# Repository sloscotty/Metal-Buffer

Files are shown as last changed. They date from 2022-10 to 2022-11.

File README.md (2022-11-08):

# Metal Buffer (for ERCF or other MMU)

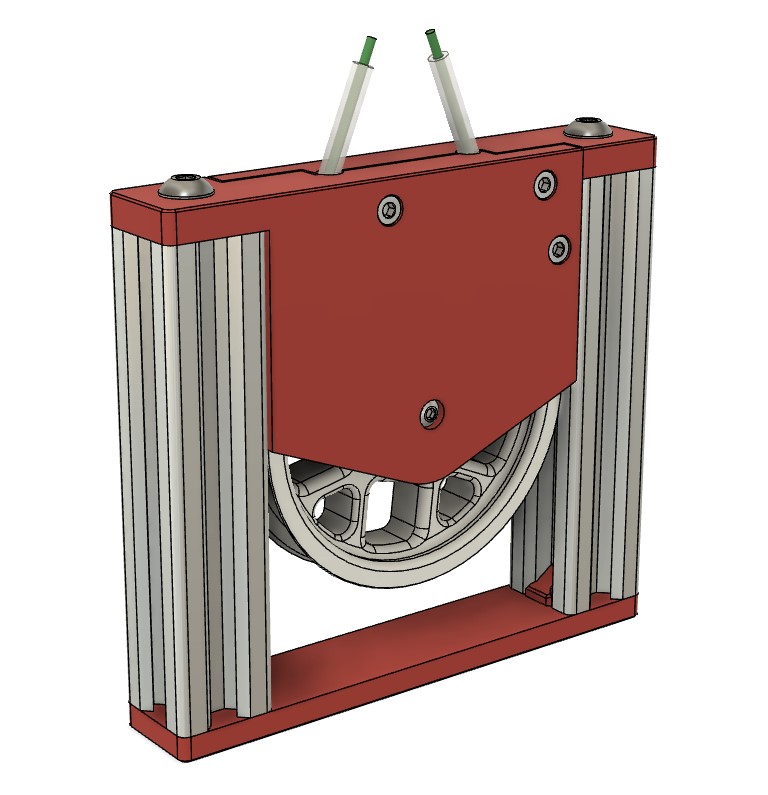
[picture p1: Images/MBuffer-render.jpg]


This is a single-loop buffer that utilizes aluminum extrusion to constrain the filament within the buffer.  It is designed around Openbuilds V-slot extrusion because I had tons of it around.  It also uses the buffer wheel and bearing from the Enraged Rabbit Carrot Feeder project.

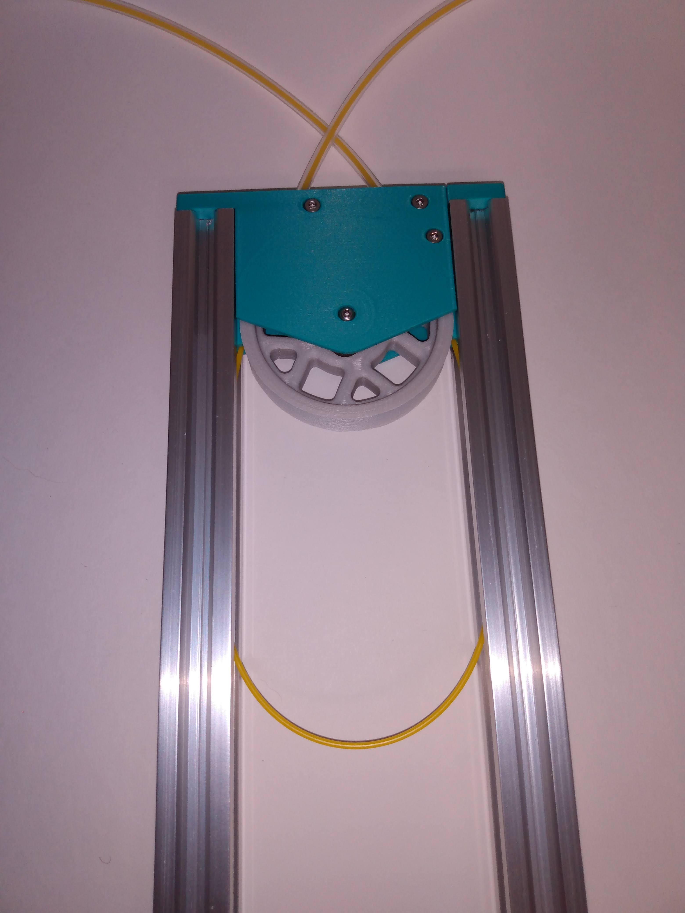
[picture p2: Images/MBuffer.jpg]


The design could probably be modified to work with other 20x20 extrusion, but it would not be a trivial task.  The slot in the top wheel assembly depends on the extra space made available by the "V" slot.  Additionally, the tapered slot provides a natural guide for the filament once it leaves the printed wheel assembly.

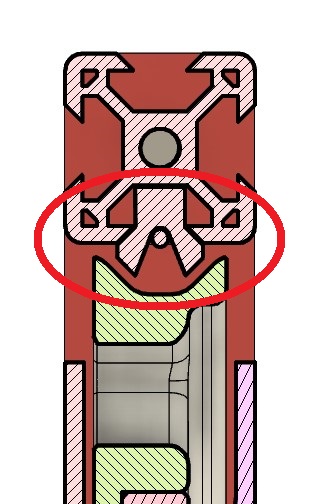
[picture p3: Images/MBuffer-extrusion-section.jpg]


For you ERCF users, V-slot is available in 20x60 (enough for 3 buffers) for about $20/meter. And the spacing almost exactly matches the tool spacing of the ERCF. (It's also available in 20x40 and 20x80.) Here is an example of two buffers mounted in 20x40:

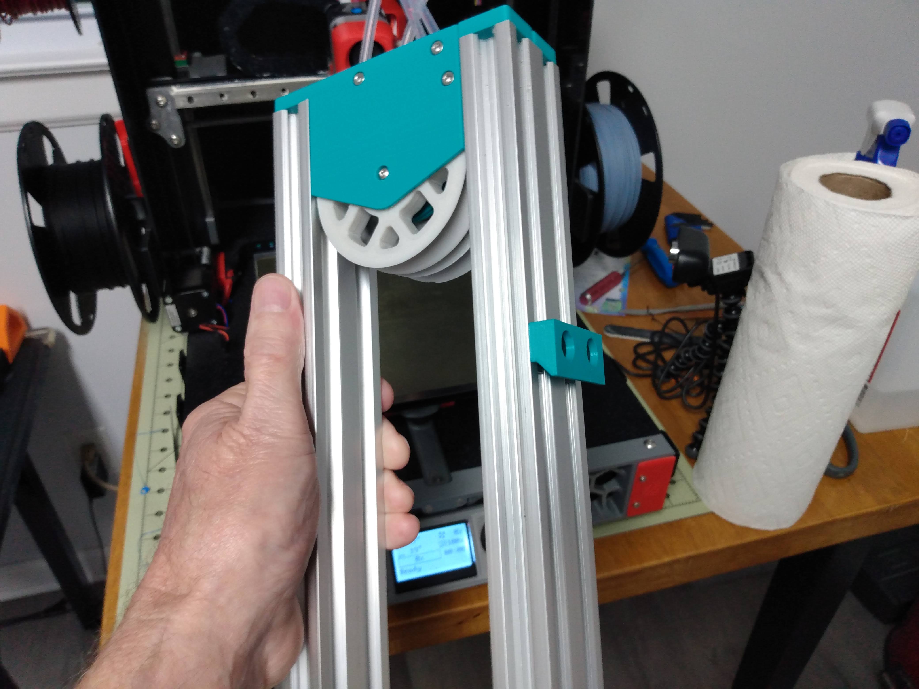
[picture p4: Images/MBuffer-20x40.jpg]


## Determine Extrusion Length

To determine the length of the extrusion required (in mm) use the formula:

**BufferLength/2 + 65** (65mm is the space used by the wheel assembly.)

To determine "BufferLength" for ERCF: add the length of the bowden tube,  the distance from the bottom of bowden tube to the nozzle, and the distance from the top of the bowden tube to the magnetic gate (35mm). Note: configured bowden to nozzle distance may not include distance between extruder gears and bowden.

For example, I'm using ERCF on a Switchwire with an LGX.  My bowden tube is 425mm,  my configured bowden-to-nozzle distance is 82mm (I allowed an additional 8mm for bowden to gears).  So "BufferLength" for me was 425 + 90 + 35 = 550.  Doing the calculations above, my requied extrusion length turned out to be 340mm.  Just to be safe, I cut my extrusions to 350mm.

## BOM (for a single buffer)
 - (2) [V-slot aluminum extrusion of required length](https://openbuildspartstore.com/v-slot-linear-rail-1/)
 - (8) M3 x 5mm x 4mm heat-set insert
 - (4) M3 x 8mm SHCS
 - (2) M3 x 10mm SHCS
 - (1) M3 x 6mm BHCS
 - (1) M3 x 8mm BHCS
 - (2) M5 x 6mm BHCS (or self-tapping screws below)
 - (2) M5 x 10mm BHCS (or thumbscrews or self-tapping screws below)
 - (2) 2.5mm ID x 4.0mm OD PTFE tubes (of appropriate length)
 - (1) 608ZZ Bearing (from ERCP)

### (options)
 - M5 x 0.80 tapping tool (for tapping extrusion)
 - (2) M5 x 10mm x 16mm diam thumbscrews [on amazon](https://www.amazon.com/dp/B07KFV6HW8/) (must be tapped with tool)
 - (4) [#10 x 3/4" Self-Tapping Screws](https://openbuildspartstore.com/self-tapping-screw/) (in case you don't like tapping)
 
**Note 1:** You can use a bit longer screws (1-2mm) than shown **except** for the M3 BHCS (axle screws).

**Note 2:** The top assembly *clamps* the PTFE tubing in place. Use of less than 2.5mm ID risks "choking" the filament.

## Directions

Print the parts using standard Voron settings (40% infill, 0.2 layerheight, 0.4 forced extrusion width) out of ABS or ASA.

The Documentation folder contains the [assembly instructions](./Documentation/MBuffer-Assembly.pdf).

## Loading the Buffer

The top of the buffer assembly can be removed for loading if required.  Depending on how you mount your array of buffers, the buffer can be loaded without removing the top.

Here are three modules, each with two buffers mounted in 20x40 extrusion. Each module will stay together even with one top removed for loading.  However, I usually load without removing a top (or even lifting a module - I can reach to the middle of my array easily enough).

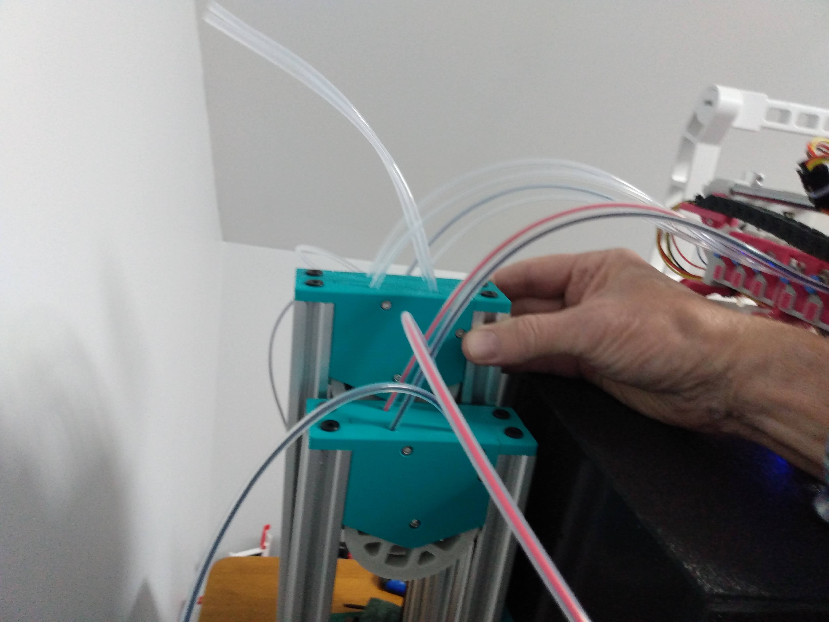
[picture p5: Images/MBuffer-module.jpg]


## How it works and mounting recommendations/caveats (example: MBuffer on Switchwire with 6-cart ERCF)

The filament paths in the buffer's top-assembly are actually straight (as shown in the cross-section). This forces the filament to the extrusion during unloading. Ideally, the resulting tension causes the filament to stay in both extrusions during the load and unload.

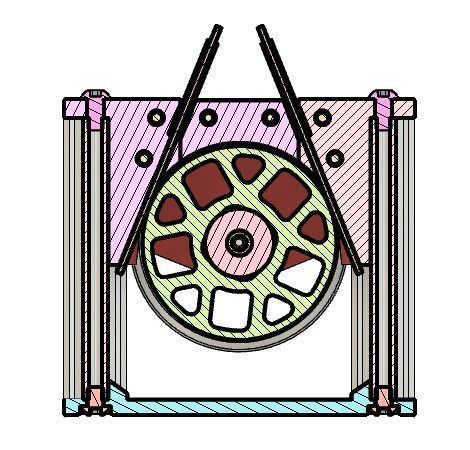
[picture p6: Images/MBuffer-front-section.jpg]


However, excessive "twisting" of the filament (from elsewhere in the system) can cause the filament to pop out of the extrusion.  Therefore positioning the buffer in order to reduce filament twist is essential.  Ideally you want the buffer assembly to be mounted directly behind the ERCF with each buffer aligned with one of the carts.  Even better if you can have your spools mounted behind the buffers.

Here is my current mounting on Switchwire.

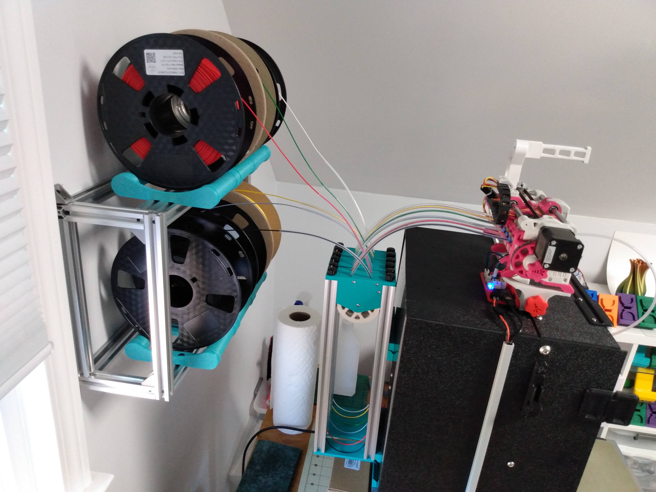
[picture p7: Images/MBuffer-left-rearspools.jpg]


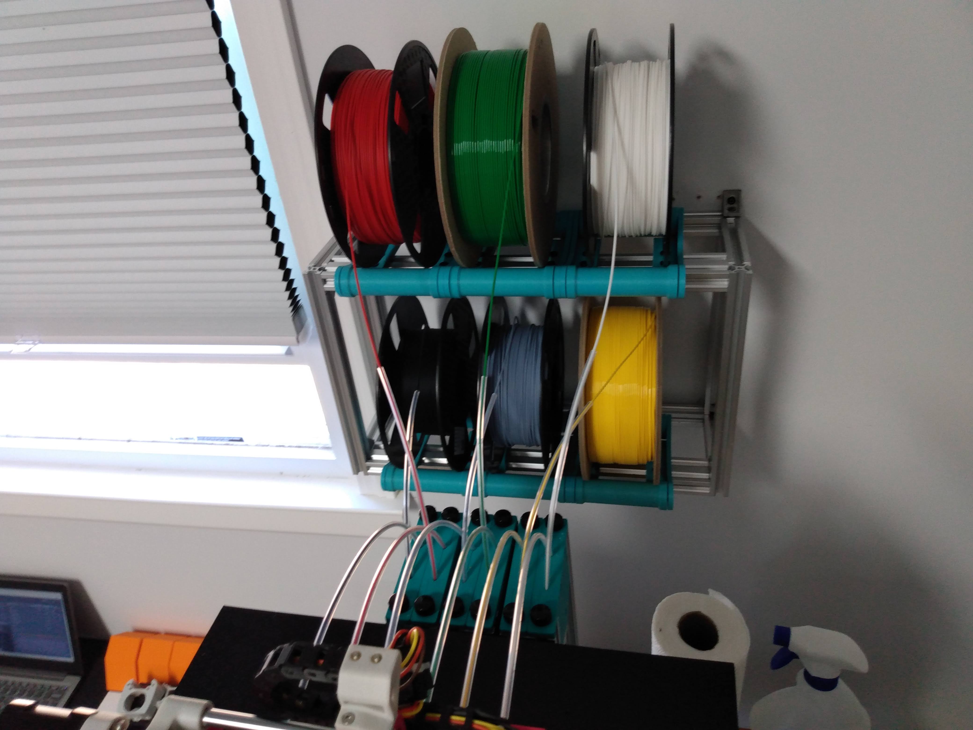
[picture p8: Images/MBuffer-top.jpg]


I originally had my spools routed to the buffers from the sides, but never did have problems with popping filament.  But I am only buffering ~600mm of filament.  A V2 buffering 1100-1200mm will require more care.  Thanks to garbqgebag on discord for beta-testing this design with a V2 and pointing out the importance of mounting position.  See our discussion on the Voron discord: https://discord.com/channels/460117602945990666/909743915475816458/1039285958933225603

### And finally, Metal Buffer in action!

https://user-images.githubusercontent.com/12124123/196645301-cd481165-e586-41fb-b28d-ce4f89cd5ee8.mp4

Enjoy!

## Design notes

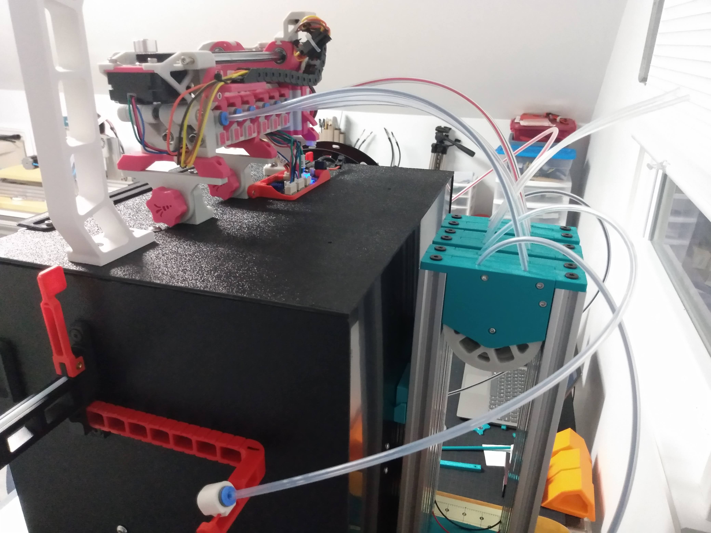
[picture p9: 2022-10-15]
Images/MBuffer-right.jpg

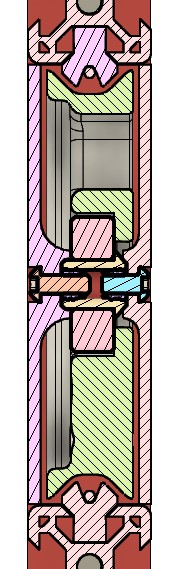
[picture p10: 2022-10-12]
Images/MBuffer-cross-section.jpg

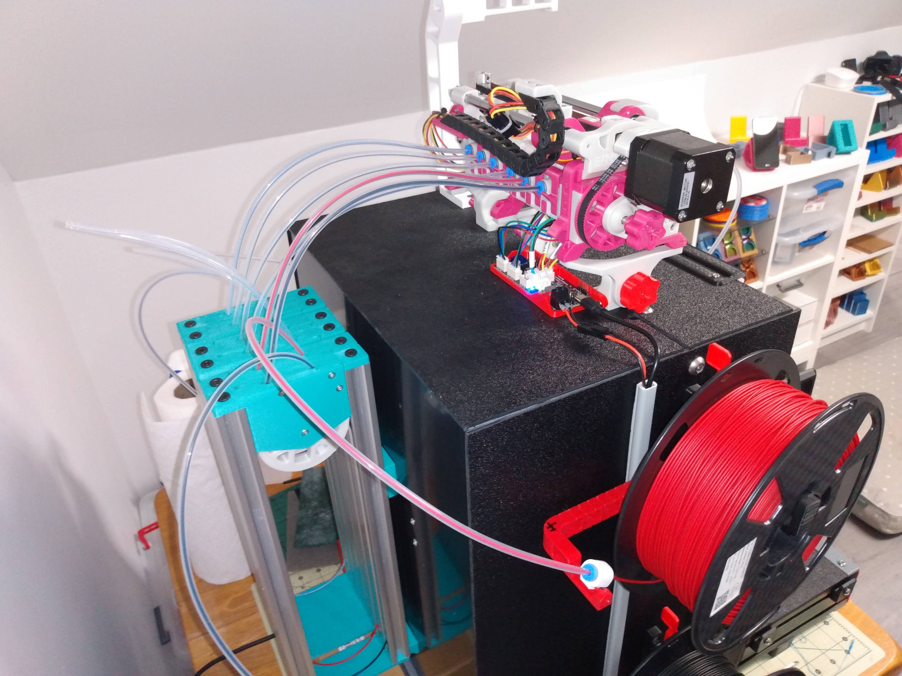
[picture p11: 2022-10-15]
Images/MBuffer-left.jpg

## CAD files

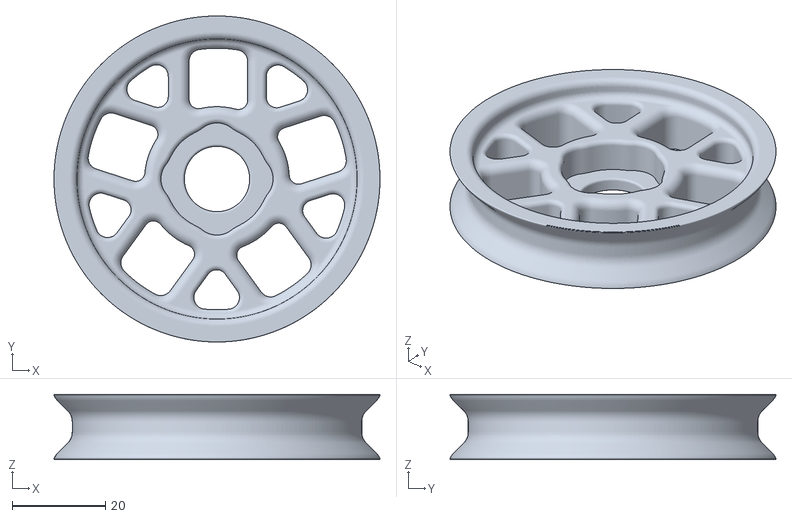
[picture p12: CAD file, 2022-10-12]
STLs/ERCP-Buffer-Wheel/[a]_Buffer_Wheel.stl
69.8 x 69.8 x 14.0

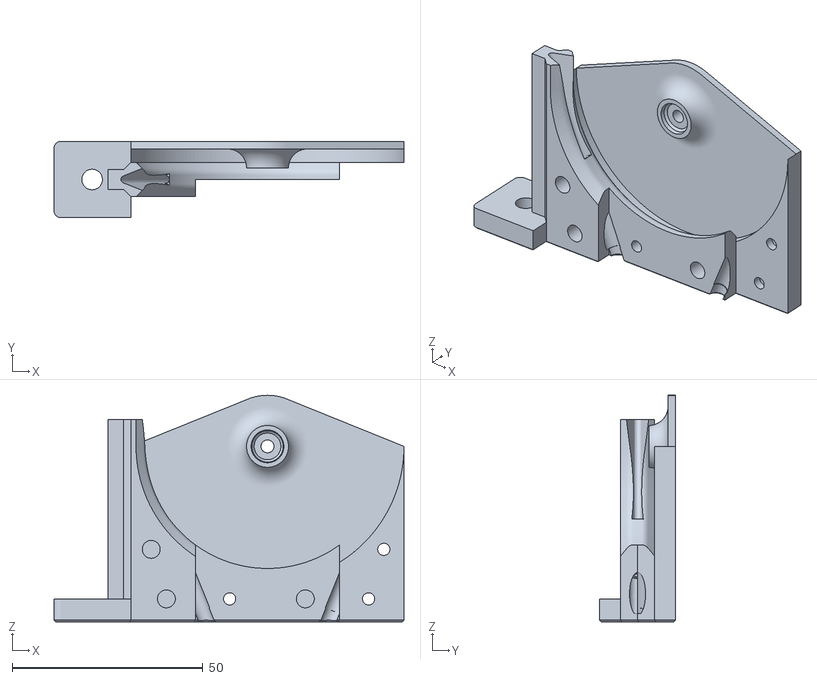
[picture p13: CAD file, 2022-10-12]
STLs/MBuffer-Top-5mm-hub.stl
91.8 x 20.0 x 59.4

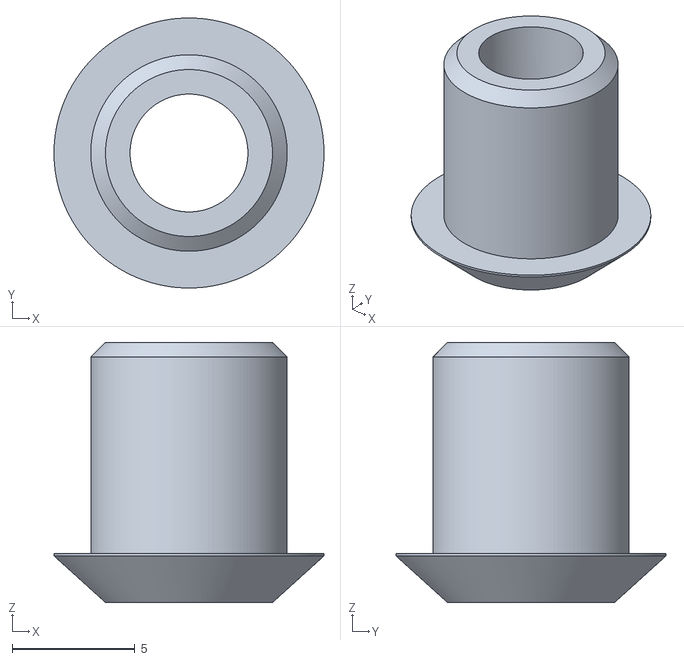
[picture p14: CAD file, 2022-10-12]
STLs/MBuffer-Axle.stl
11.0 x 11.0 x 10.6

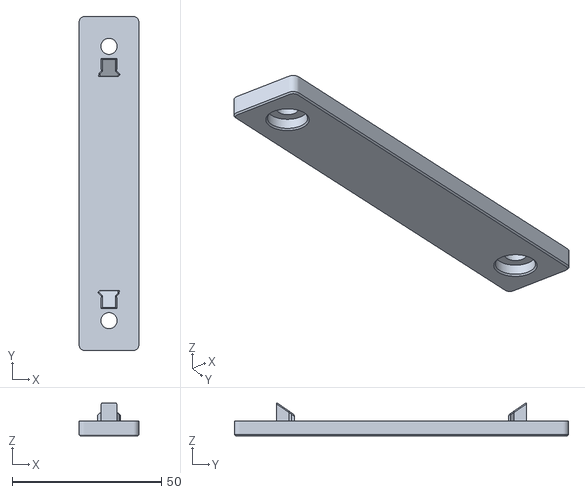
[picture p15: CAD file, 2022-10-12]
STLs/MBuffer-Bottom.stl
20.0 x 112.0 x 11.0

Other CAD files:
STLs/MBuffer-Top-2mm-hub.stl
CAD/Metal Buffer.f3d

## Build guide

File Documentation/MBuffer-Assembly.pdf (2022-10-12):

# Metal Buffer Assembly Instructions

## Prepare Parts

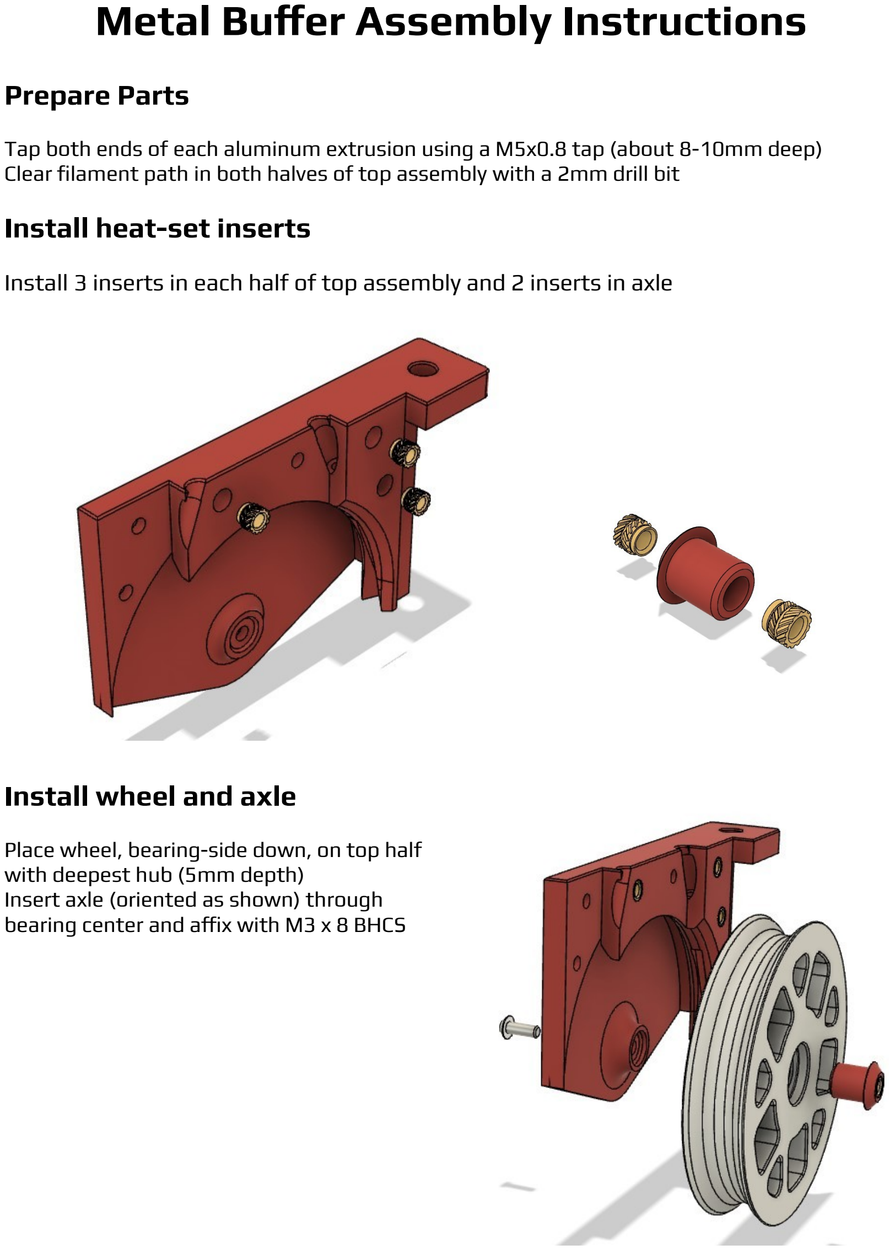
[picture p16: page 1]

Tap both ends of each aluminum extrusion using a M5x0.8 tap (about 8-10mm deep) Clear filament path in both halves of top assembly with a 2mm drill bit

## Install heat-set inserts

Install 3 inserts in each half of top assembly and 2 inserts in axle

## Install wheel and axle

Place wheel, bearing-side down, on top half with deepest hub (5mm depth)
Insert axle (oriented as shown) through bearing center and affix with M3 x 8 BHCS

## Assemble top of buffer

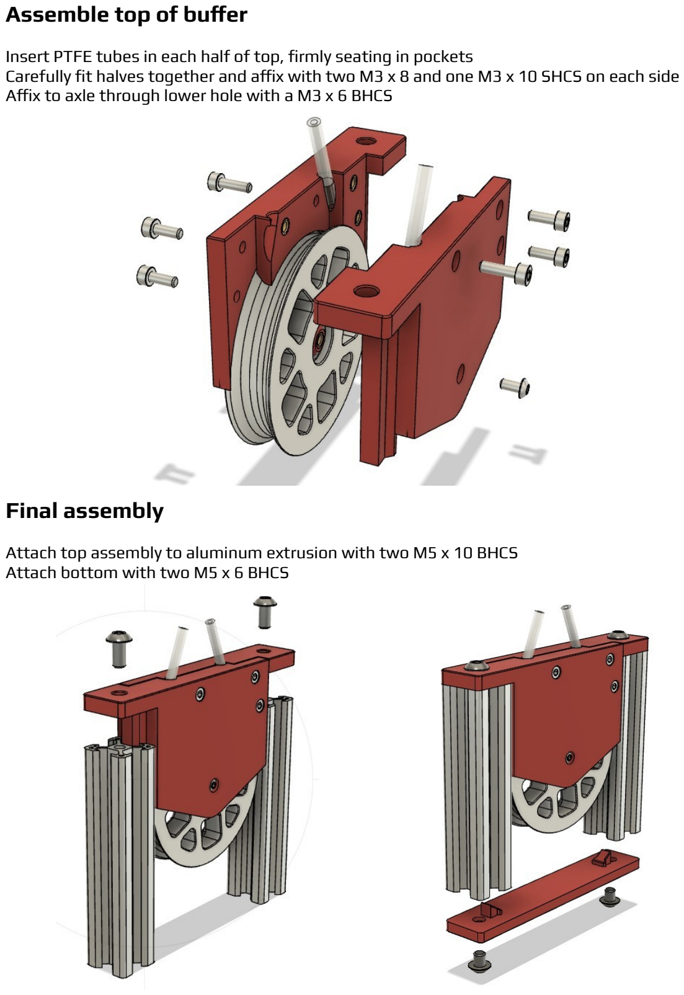
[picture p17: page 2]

Insert PTFE tubes in each half of top, firmly seating in pockets
Carefully fit halves together and affix with two M3 x 8 and one M3 x 10 SHCS on each side Affix to axle through lower hole with a M3 x 6 BHCS

## Final assembly

Attach top assembly to aluminum extrusion with two M5 x 10 BHCS Attach bottom with two M5 x 6 BHCS
